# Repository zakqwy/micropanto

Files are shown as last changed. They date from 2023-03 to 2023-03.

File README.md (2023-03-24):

# MicroPanto

MicroPanto is a 50:1 pantograph reducer that converts a desktop CNC router into a micro-engraver. The machine is driven by a [Handibot](https://www.shopbottools.com/products/handibot), whose working range is shrunk to a few millimeters with a corresponding increase in resolution. A microswitch temporarily mounted to the Handibot's Z-axis actuates a stylus which can be electronically adjusted for different workpiece heights. The working tool is a laser-turned diamond bonded to a strip of stainless shim stock with a tip radius of roughly 2 microns. After assembling the machine at Haystack, a number of substrates (polished stone, steel, obsidian, gold-coated glass, silver, rice, etc) were micro-engraved with tiny messages and designs.

[project video link](https://player.vimeo.com/video/579890845) (thanks Jack!)

[a more detailed engraving video](https://youtu.be/u6EFz45_r_Y)

_Machine temporarily installed in the Haystack Metal Shop:_
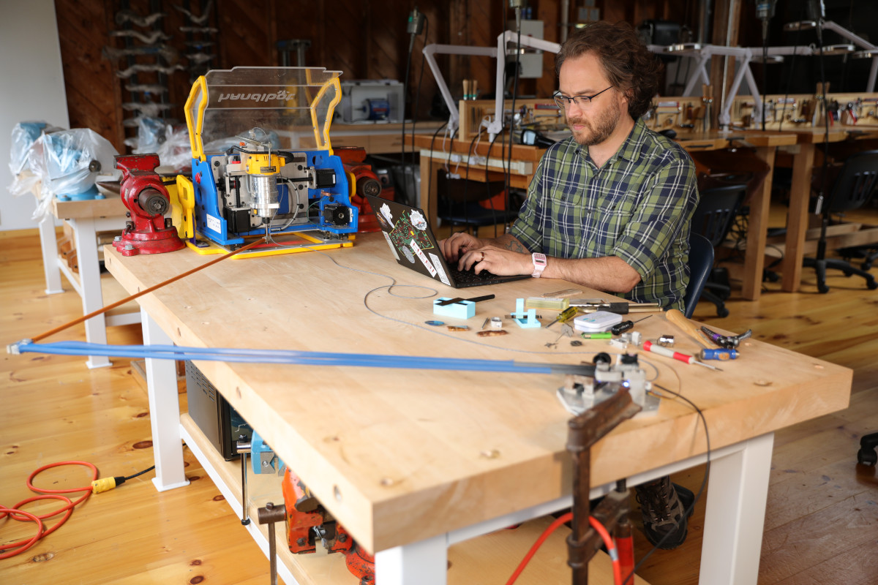
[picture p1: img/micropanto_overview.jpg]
micropanto_overview


_"Too Many Potatoes" engraved on a gold-coated slide, with 1/64" end mill for scale:_
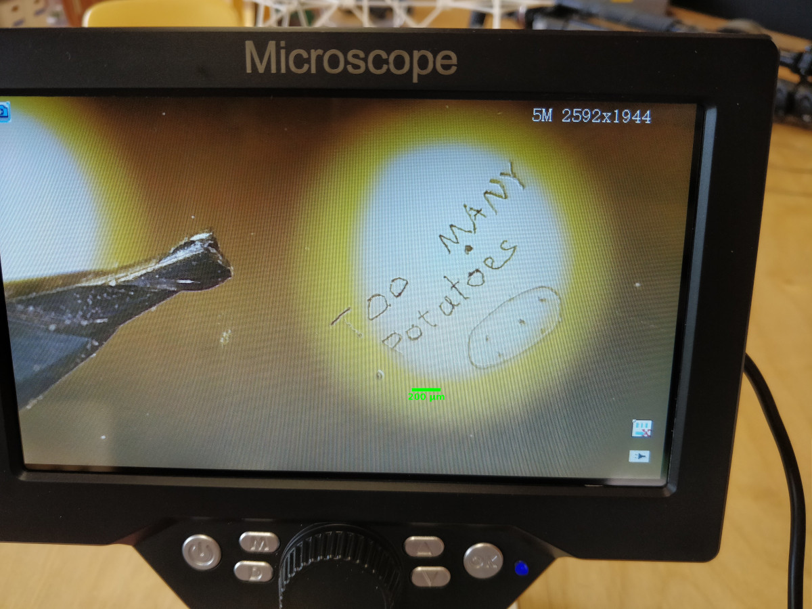
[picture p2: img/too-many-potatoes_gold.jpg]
too-many-potatoes_gold


_Stylus end showing base plate, work in vise, servo for stylus actuation, stylus control PCB, and modular superelastic flexure linkages:_
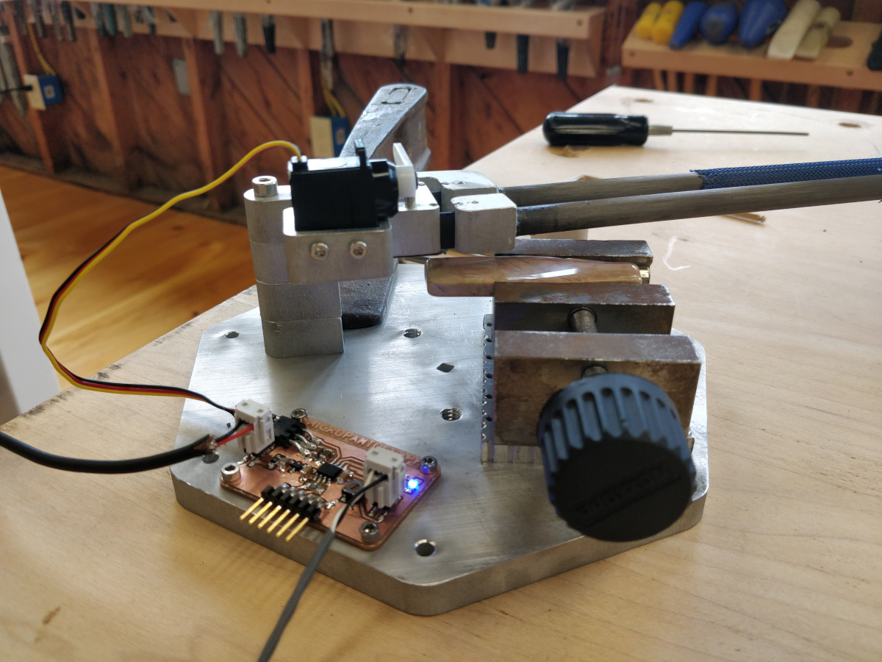
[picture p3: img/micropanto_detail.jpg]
micropanto_detail


This work may be reproduced, modified, distributed, performed, and displayed for any purpose, but must acknowledge the orginal project. Copyright is retained and must be preserved. The work is provided as is; no warranty is provided, and users accept all liability.

© zach fredin, massachusetts institute of technology, 2021

## micro-engraving
We tried micro-engraving a number of different things at Haystack. Here is a summary:

|thing|notes|
|---|---|
|gold-coated glass slide|Worked fairly well if stylus pressure was adjusted properly. Delicate during handling, somewhat impractical.|
|polished stone|Sourced from Ellen's collection (thanks Ellen!). Maybe picture jasper? Engraved fairly well, a bit of chipping if pressure too high. Required inking to see marks.|
|obsidian|Chips quite a bit. Looks promising if pressure can be better controlled; not great as-is.|
|aluminum|Snapped the diamond off the stylus! Likely an epoxy problem rather than a material issue; diamond re-affixed with CA and no further breakages.|
|silver|Looks _great_, especially if silver is polished and patinaed prior to marking.|
|black oxide coated steel|Tested on a few pairs of parallel-jaw pliers. Looks good, excellent detail.|
|pearl|Roundness is challenging. Needs careful pressure control to avoid over-engraving. Not great with current stylus design.|
|dry rice|Shockingly good, but did require inking afterwards. Maybe the marks would pick up extra staining in a pilaf and become visible (and stay edible)?|
|painted steel|i.e Zach's new glasses frames. Worked fairly well, paint was a bit thick which affected resolution. Underlying scratches on steel base are probably quite fine.|
|brushed stainless|Excellent detail; difficult to see.|

Perhaps not surprisingly, the 50:1 reduction ratio combined with my hesitency to push the machine's working range meant many of the engravings were quite difficult to see, even with a 10x loupe. Neil brought a cheap electronic microscope which I photographed; in retrospect, I should have found a micro SD card and pulled images directly off the instrument. Jack also got a few pictures with his amazing macro lens setup. As I find time, I'll use our instruments at CBA to get better images and update the gallery below.

_"The Center for Bits 'n Atoms", poorly mouse-drawn on the Handibot's SmoothSketch App:_
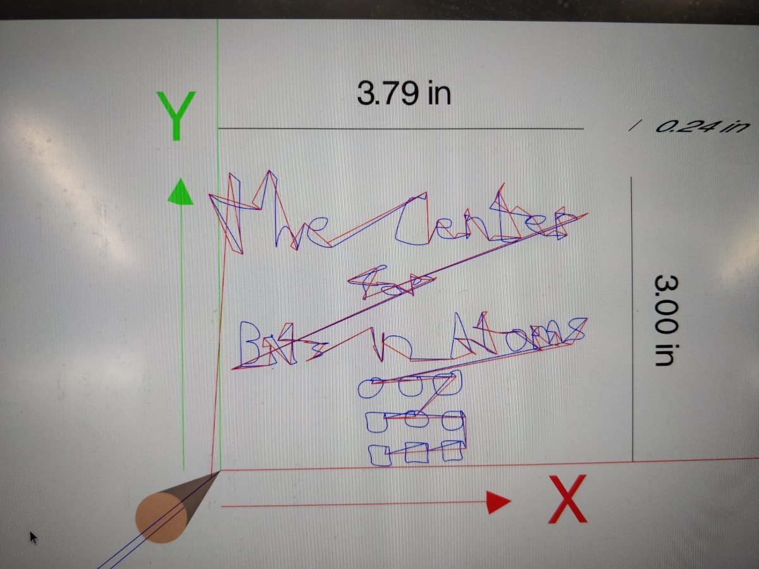
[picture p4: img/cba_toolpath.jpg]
cba_toolpath


_The resulting engraving on polished stone, after inking to add contrast. The "o" in Atoms is roughly 100 microns in diameter, the same as a typical strand of hair:_
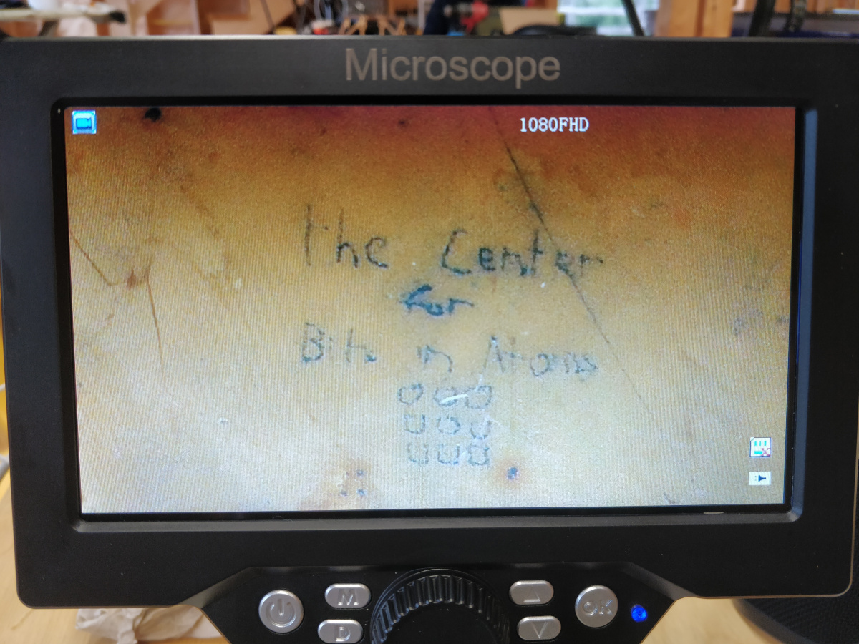
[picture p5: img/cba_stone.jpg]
cba_stone


_"Too Many Potatoes" rendered in inked stone:_
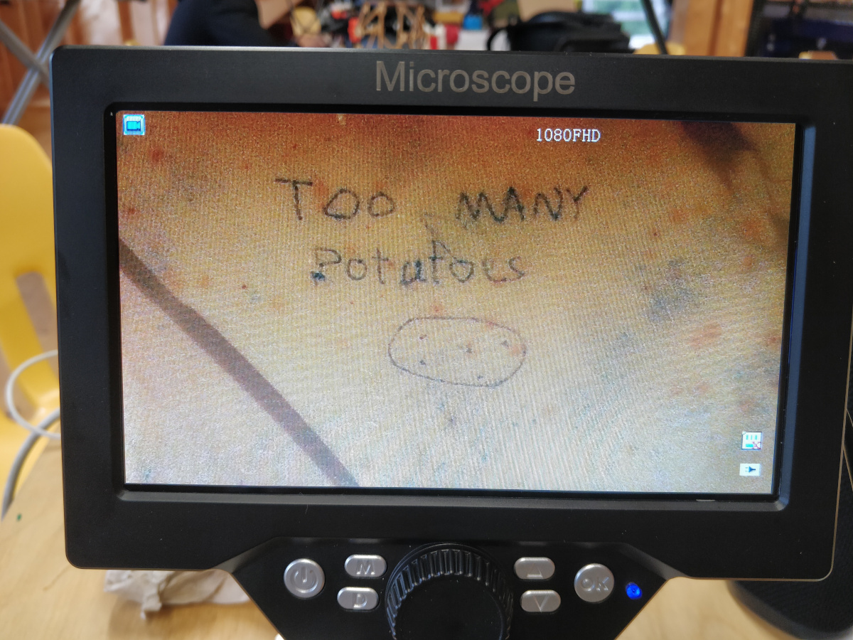
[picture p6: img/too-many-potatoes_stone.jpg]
too-many-potatoes_stone


_One of Andrea Dezsö's Forest Beings in gold-coated glass:_
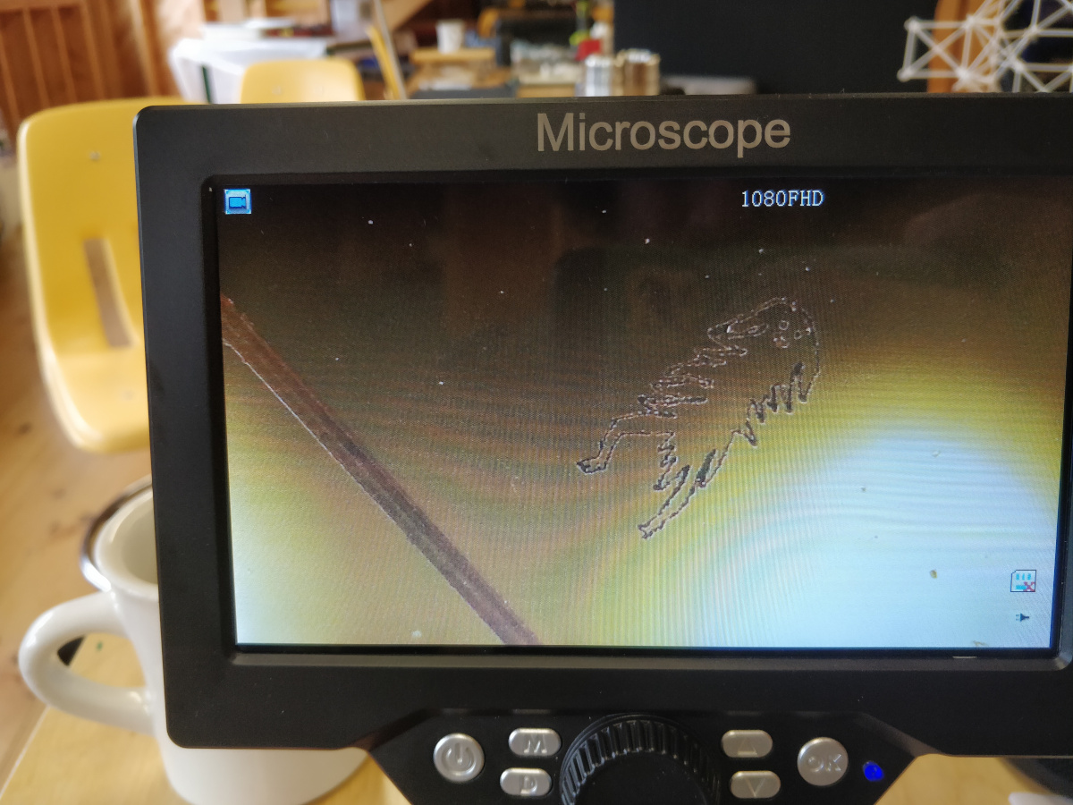
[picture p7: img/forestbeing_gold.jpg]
forestbeing_gold


_... and again in inked stone:_
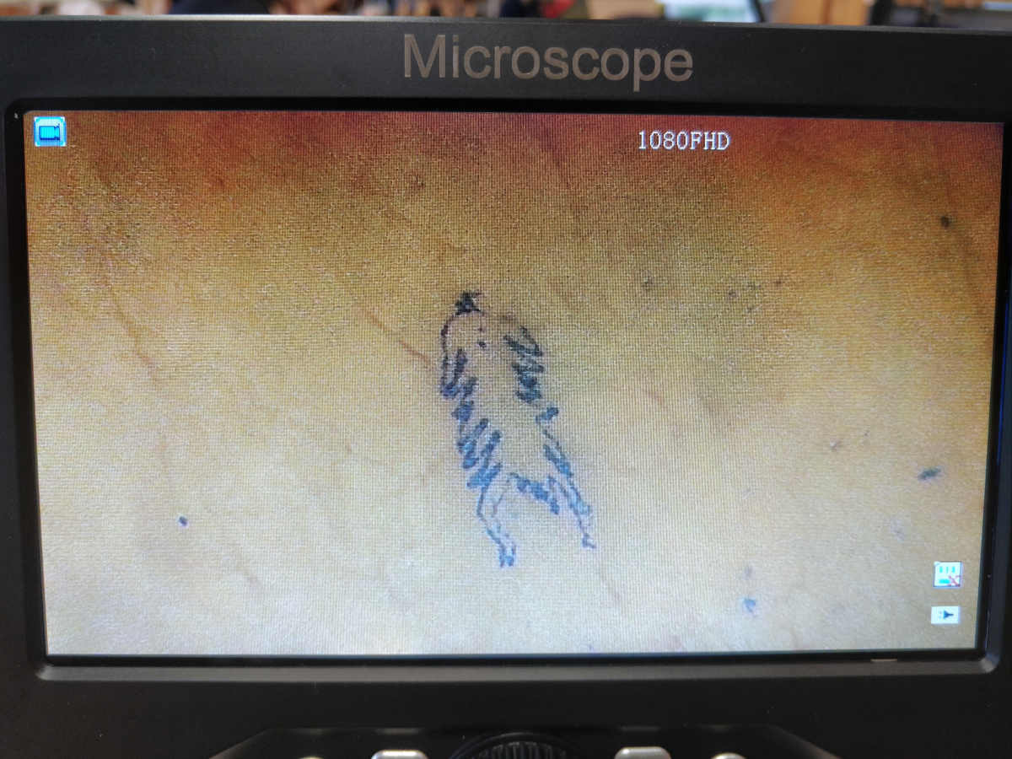
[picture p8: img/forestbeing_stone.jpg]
forestbeing_stone


_... and finally on grains of inked rice, along with a "HAYSTACK" sign:_
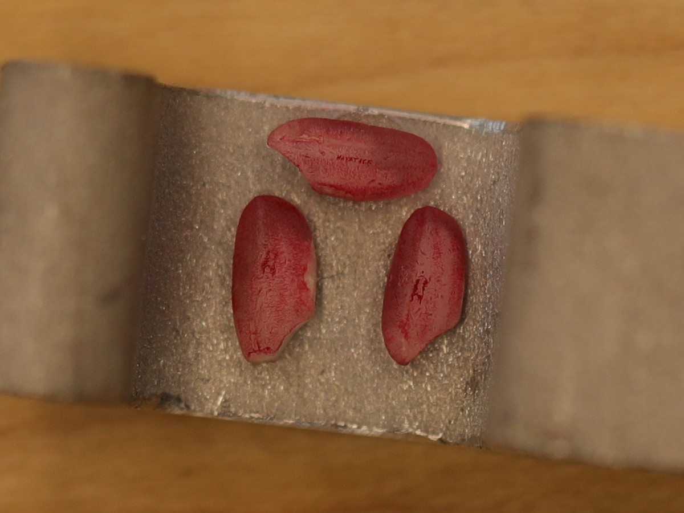
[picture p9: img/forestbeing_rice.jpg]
forestbeing_rice


_A Haystack welcome message (and another CBA "logo") in inked stone:_
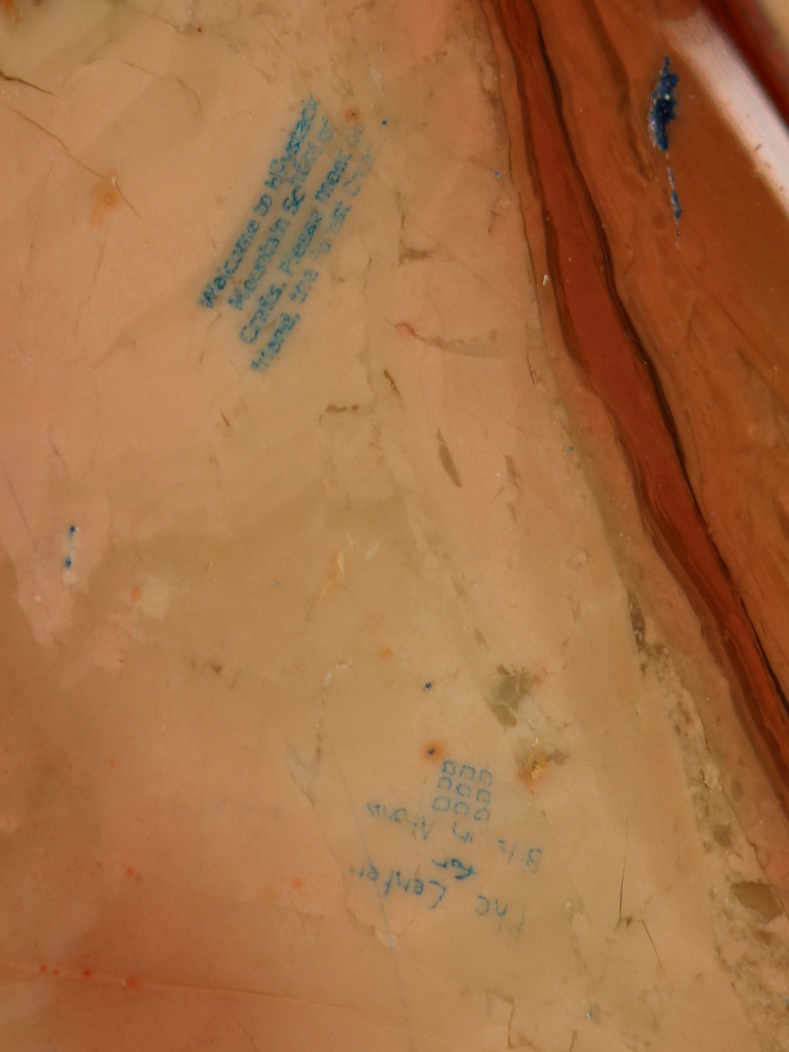
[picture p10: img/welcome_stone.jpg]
welcome_stone


_Lauren Fensterstock's black hole drawing, later micro-engraved on a number of substrates:_
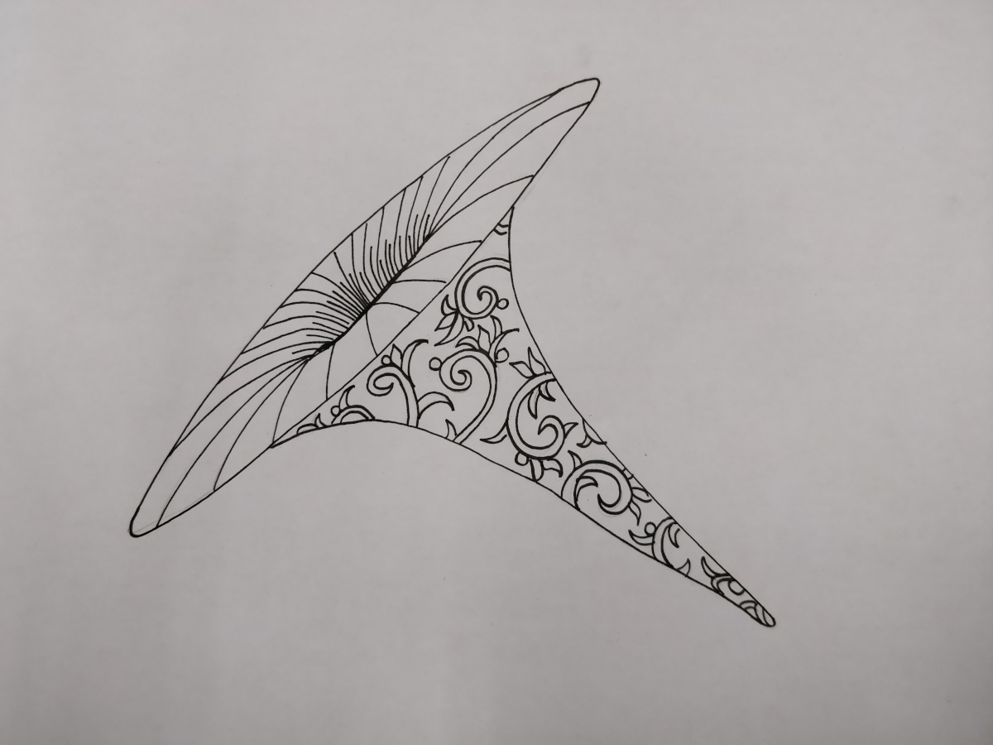
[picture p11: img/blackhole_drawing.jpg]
blackhole_drawing


_Black hole rendered on parallel-jaw pliers, with scale bar:_
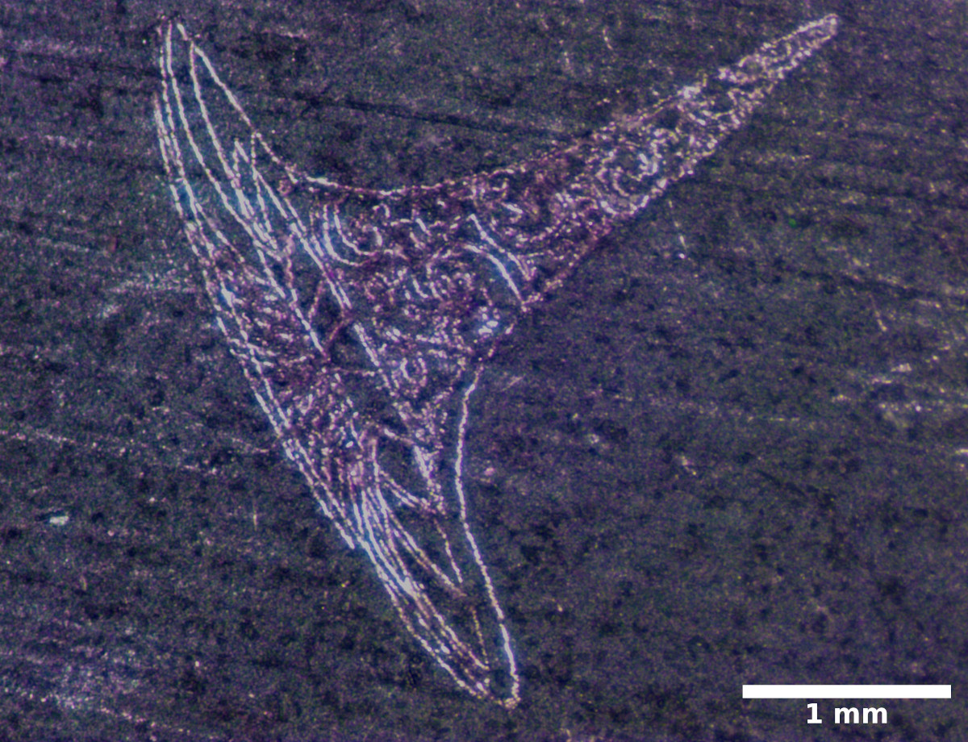
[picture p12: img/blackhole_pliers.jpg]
blackhole_pliers


_Zoomed out black hole for reference:_
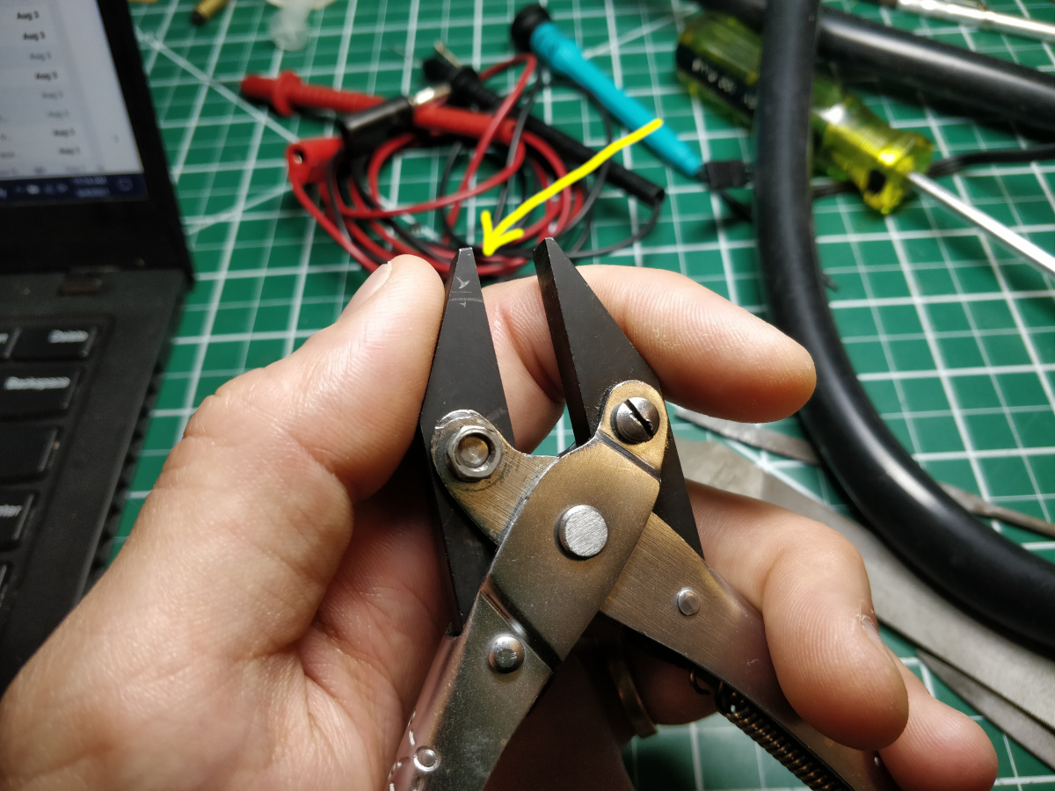
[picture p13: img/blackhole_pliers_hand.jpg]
blackhole_pliers_hand


_"Too Many Potatoes" on my new glasses frames, without magnification to show scale:_
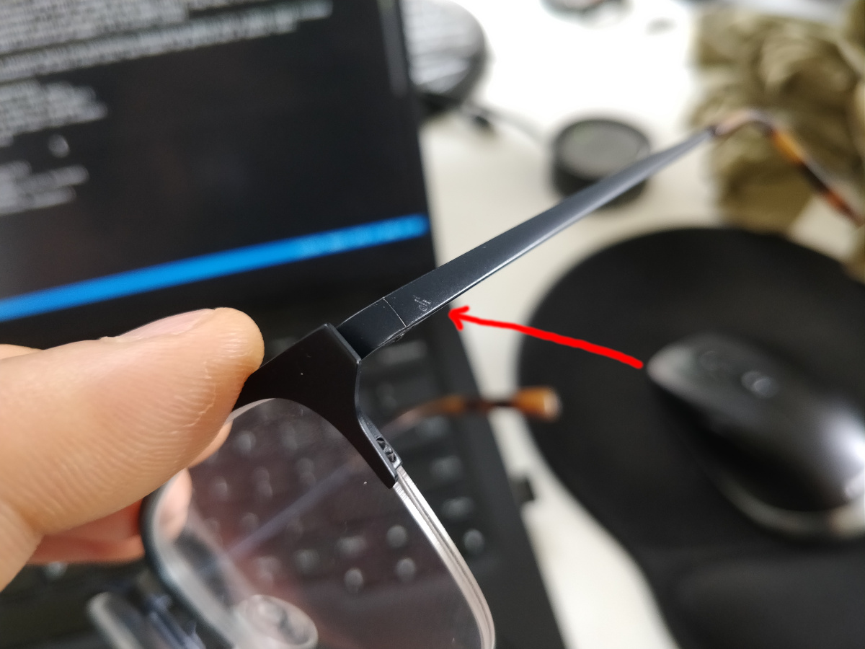
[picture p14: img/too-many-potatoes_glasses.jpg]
too-many-potatoes_glasses


## machine design
More information forthcoming... for now, [ecad](ecad) for the stylus control PCB, [firmware](firmware) for the stylus control firmware, and [mcad](mcad) for the mechanical design files. Parts are fabricated as follows:

|part|method|
|---|---|
|aluminum structural parts|waterjet, drill press|
|nitinol flexures|wire-EDM|
|stylus flexure|laser micro-machining|
|diamond stylus|laser micro-turning|
|PCB|desktop router, soldering iron|
|gold-coated slides|sputter coater|
|slide case|FDM 3D printer|
|pulltruded CFRP tubes|purchased|
|final machine assembly|taper ream, ball-peen hammer, epoxy|

The machine is built from modular superelastic flexures, a concept I developed as part of a class last semester. You can read a lot more about them [here](https://fab.cba.mit.edu/classes/865.21/people/zach/index.html). 

_Stylus detail, showing diamond in down position:_
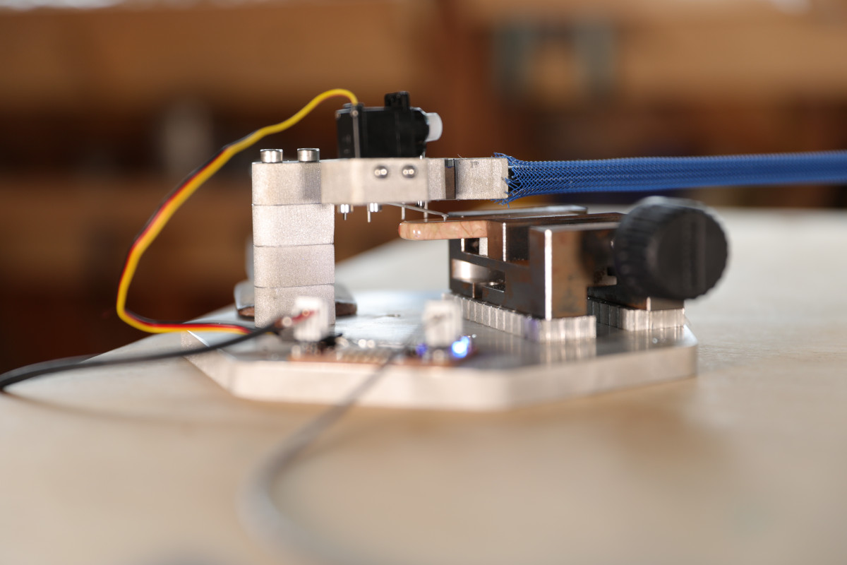
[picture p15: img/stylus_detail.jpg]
stylus_detail


_Final assembly starts with taper-reaming the waterjetted aluminum parts to match the nitinol flexures:_
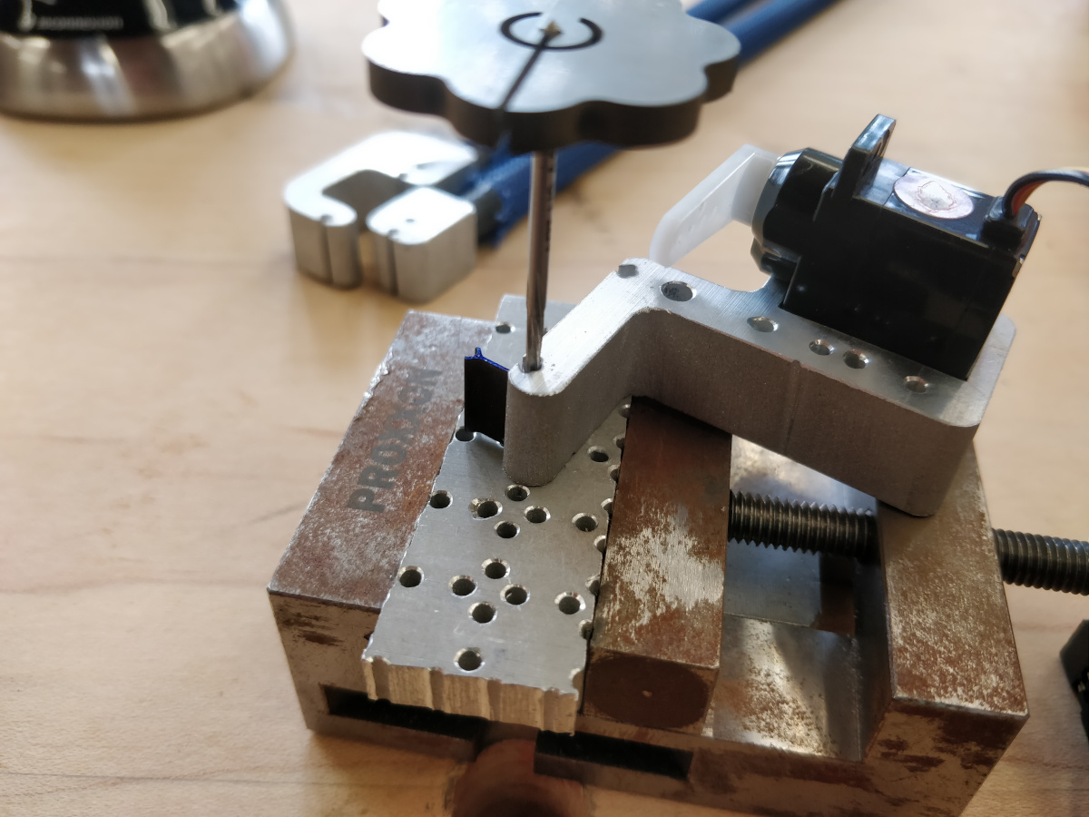
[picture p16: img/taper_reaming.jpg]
taper_reaming


_Once prepared, the joints are assembled by tapping in 7/0 taper pins with a ball peen hammer:_
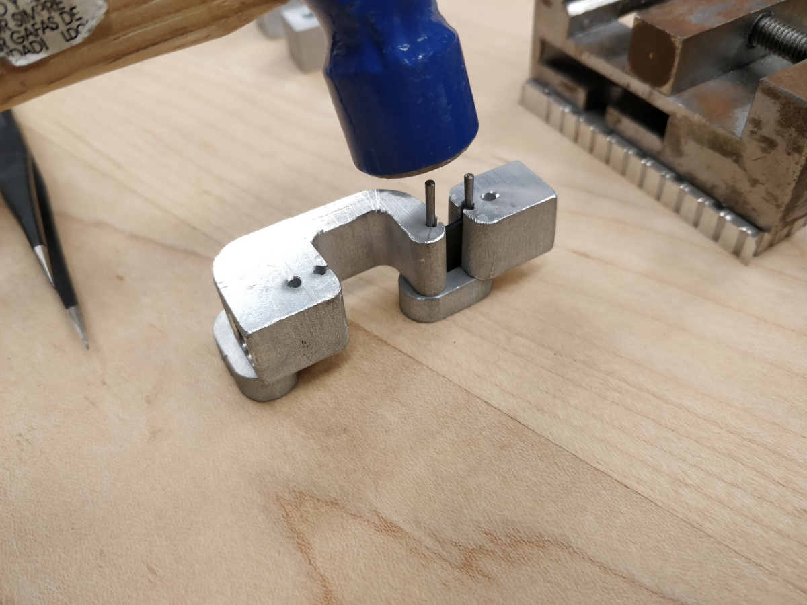
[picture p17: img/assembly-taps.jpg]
assembly_taps


_Disassembled stylus flexure and diamond (near tweezer tip) after breakage due to adhesive failure. Re-secured with cyanoacrylate, which worked well:_
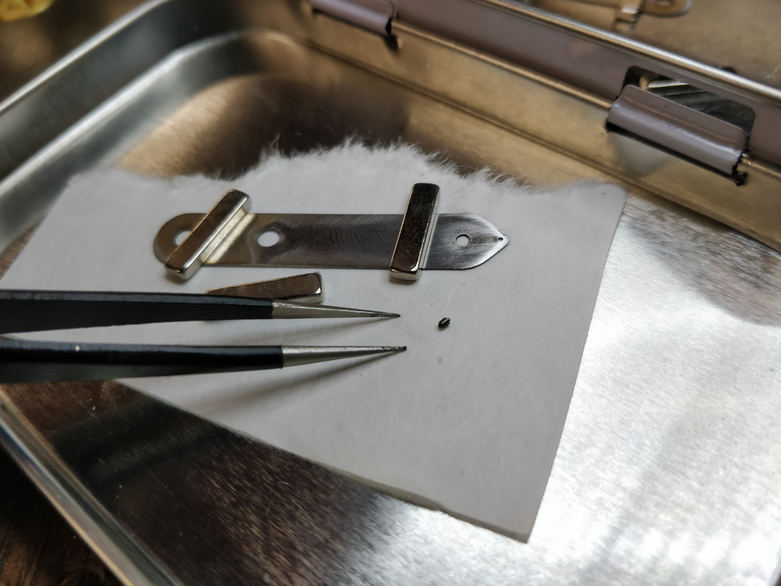
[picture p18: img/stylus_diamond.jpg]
stylus_diamond


_SEM micrograph of laser-turned diamond stylus, showing rough cut overall shape and finish pass at tip:_
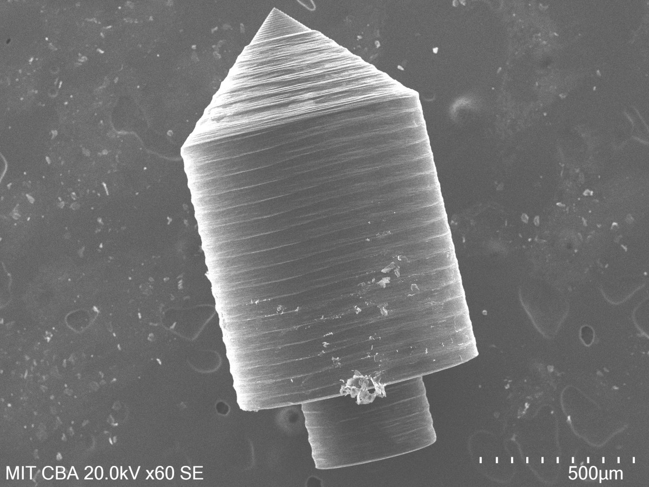
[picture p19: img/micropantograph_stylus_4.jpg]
micropantograph_stylus_4


_Another micrograph of the tip of the diamond, showing ~2 um tip radius. Would be worth re-imaging a used tip to see how it wears when used on different substrates:_
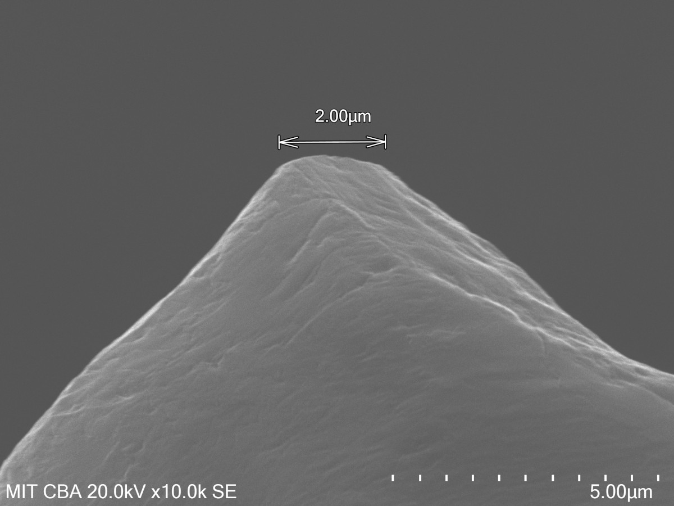
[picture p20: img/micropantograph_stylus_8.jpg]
micropantograph_stylus_8


MicroPanto roughly consists of:

|item|qty|
|---|---|
|aluminum plate, 1/2"|~75 x 75 mm|
|aluminum plate, 1/4"|~150 x 150 mm|
|aluminum plate, 1/16"|~10 x 80 mm|
|8 mm pulltruded CFRP tube|qty 3, 1 m|
|superelastic nitinol, 10 mm|~1 cc|
|bolts|~10?|
|7/0 taper pins|10|
|FR1 PCB stock|~75 x 50 mm|
|single-crystal CVD diamond|~1 x 1 x 3 mm|
|250 um stainless sheet|~10 x 40 mm|
|4 mm dowel pin|1|
|small servo motor|1|
|cable|~3 m|
|limit switch|1|
|Handibot|1|
|ATtiny412 + support components|1|
|computer|1|
|1/4" x 1/4" magnets|2|
|epoxy|a few packets|
|cable loom (for CFRP splinter protection)|~3 m|
|1/4" shaft stock|~100 mm|
|tiny vise|1|

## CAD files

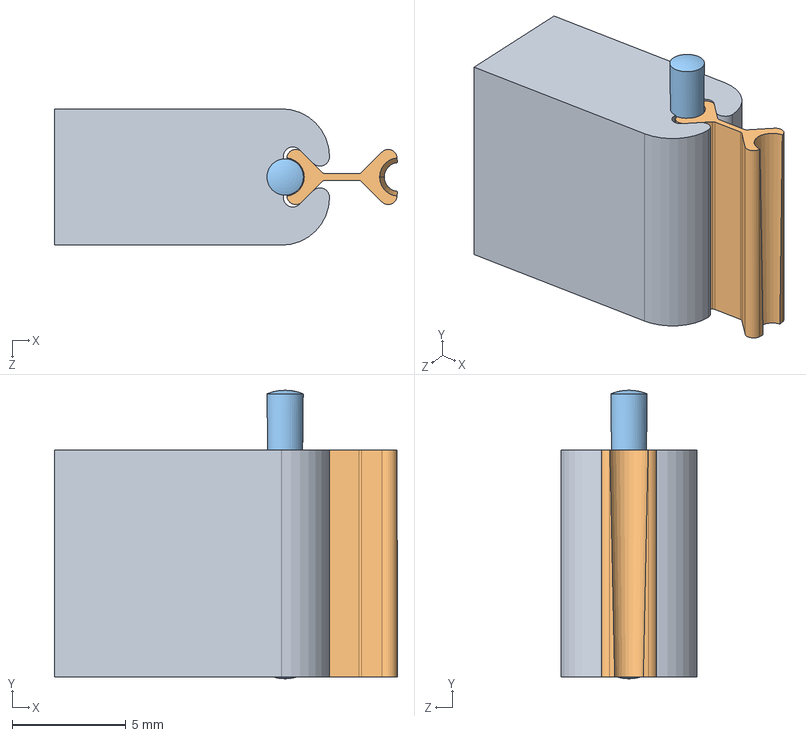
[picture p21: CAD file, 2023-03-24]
mcad/micropanto/diag.SLDASM
15.1 x 12.7 x 6.00 mm
link_long
bowtie_flexure
90681A001_18-8 STAINLESS STEEL TAPER PIN

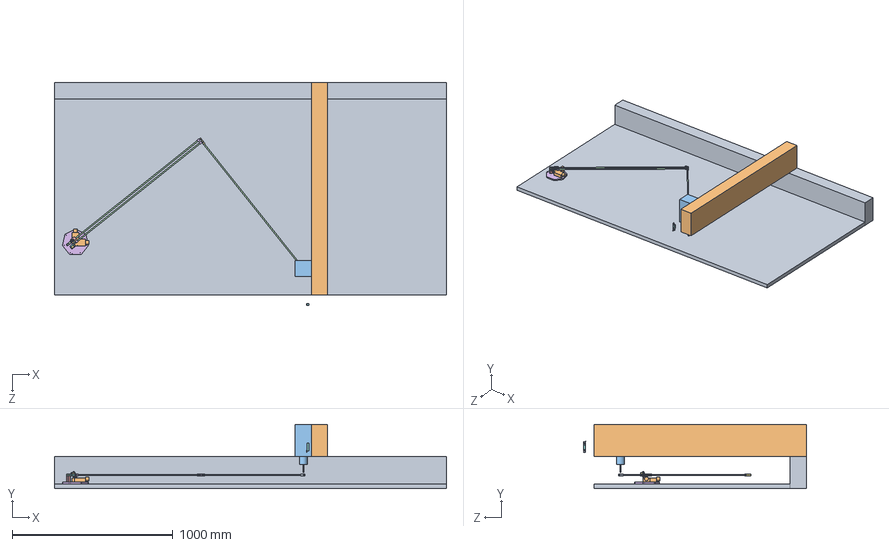
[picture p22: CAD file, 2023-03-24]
mcad/micropanto/micro-pantograph.SLDASM
2438.4 x 400.0 x 1384.9 mm
shopbot_base
shopbot_gantry
shopbot_spindle
rod_39in x 3
aluminum_adapter_1
aluminum_adapter_2 x 3
aluminum_adapter_3
aluminum_adapter_4
aluminum_adapter_5
bowtie_flexure_10_sim_part x 5
bowtie_flexure_10_sim_part2 x 5
aluminum_adapter_6
aluminum_adapter_7 x 3
base
servo
limitswitch_mount
limitswitch_bracket
proxxon_24260 x 2

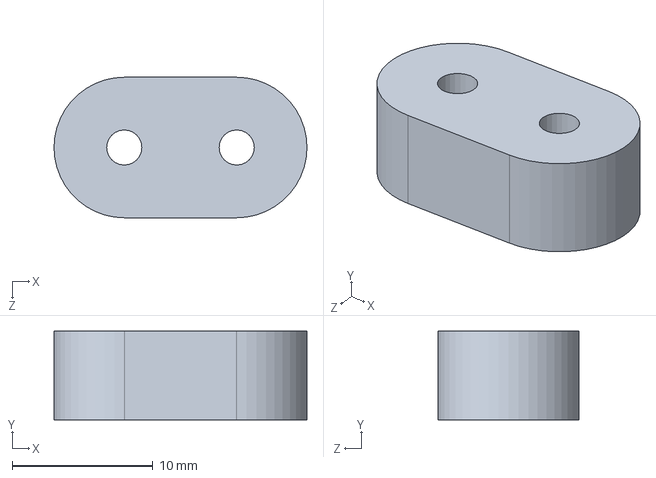
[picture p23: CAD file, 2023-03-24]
mcad/micropanto/assembly_helper.SLDPRT
18.0 x 6.30 x 10.0 mm

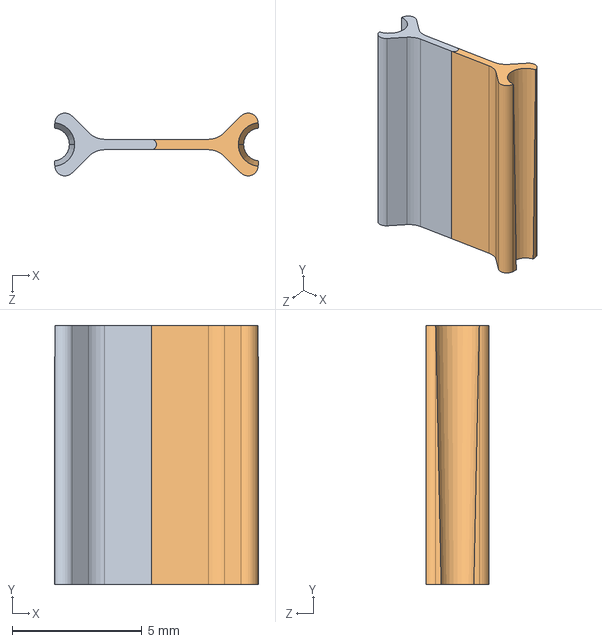
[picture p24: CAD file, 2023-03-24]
mcad/micropanto/bowtie_flexure_10_sim_assembly.SLDASM
7.89 x 10.0 x 2.43 mm
bowtie_flexure_10_sim_part
bowtie_flexure_10_sim_part2

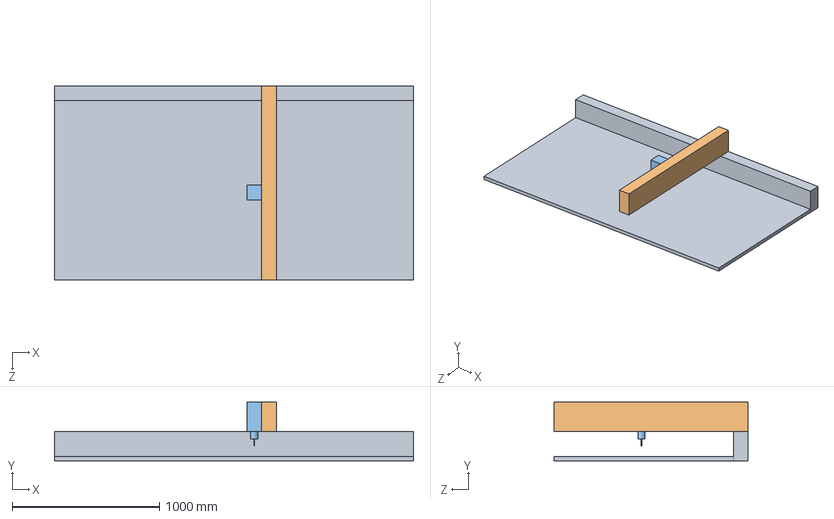
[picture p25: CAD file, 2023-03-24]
mcad/micropanto/shopbot.SLDASM
2438.4 x 400.0 x 1320.8 mm
shopbot_base
shopbot_gantry
shopbot_spindle

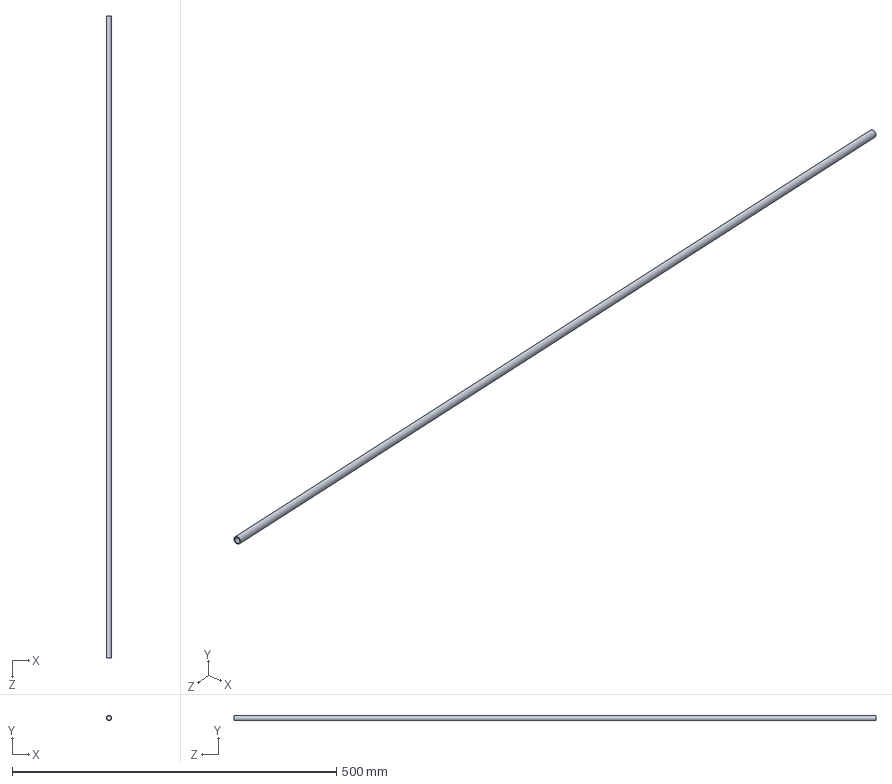
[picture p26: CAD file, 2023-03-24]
mcad/micropanto/rod_39in.SLDPRT
8.00 x 8.00 x 990.6 mm

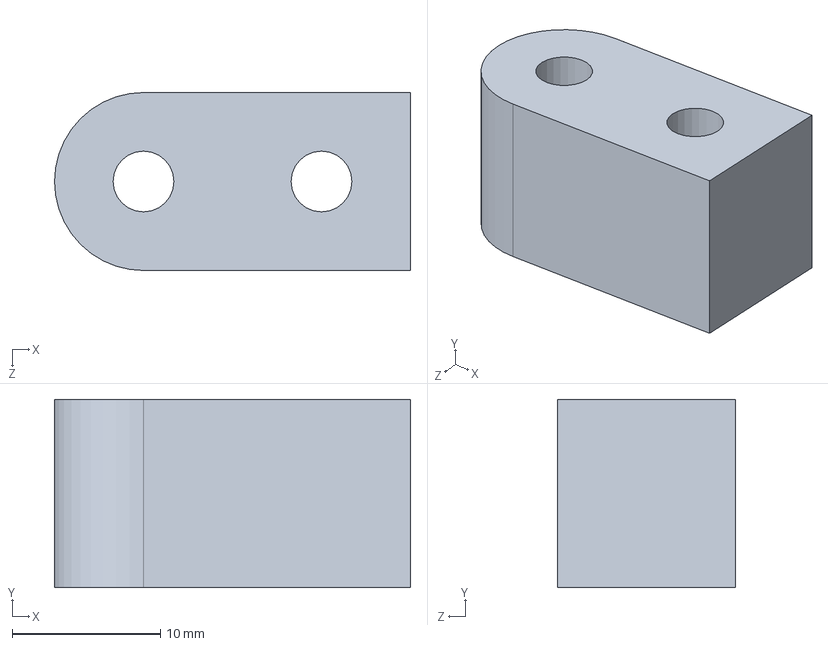
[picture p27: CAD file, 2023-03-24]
mcad/micropanto/aluminum_adapter_7.SLDPRT
24.0 x 12.7 x 12.0 mm

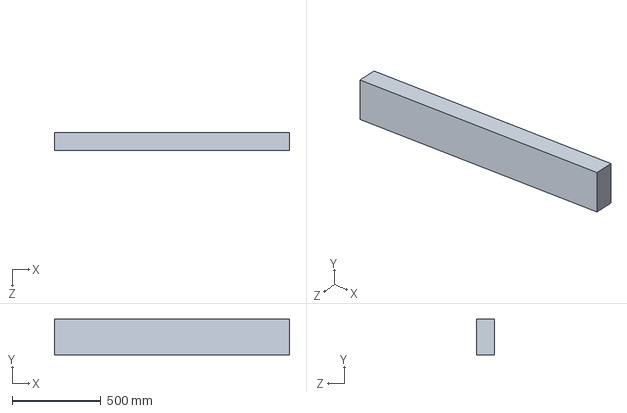
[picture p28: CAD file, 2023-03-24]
mcad/micropanto/shopbot_gantry.SLDPRT
1320.8 x 200.0 x 100.0 mm

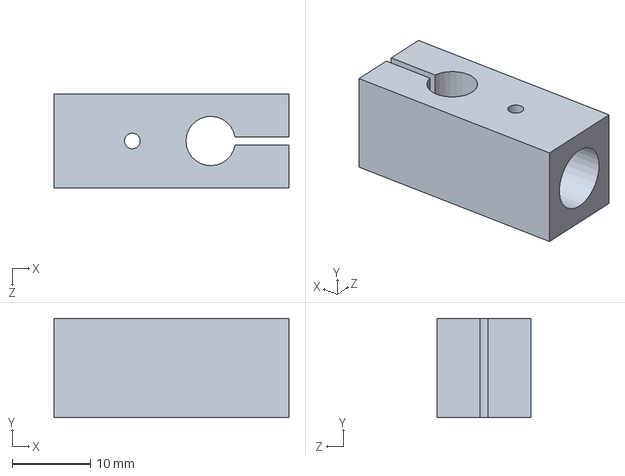
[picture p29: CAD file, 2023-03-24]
mcad/micropanto/aluminum_adapter_5.SLDPRT
30.0 x 12.7 x 12.0 mm

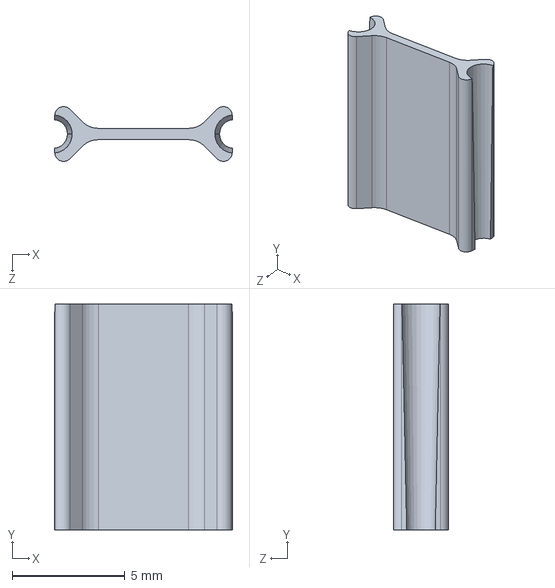
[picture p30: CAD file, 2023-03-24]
mcad/micropanto/bowtie_flexure_10.SLDPRT
7.89 x 10.0 x 2.43 mm

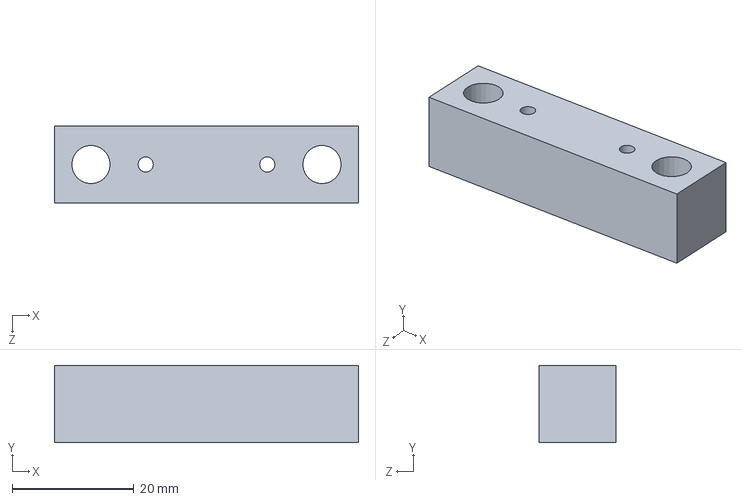
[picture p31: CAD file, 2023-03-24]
mcad/micropanto/limitswitch_mount.SLDPRT
50.0 x 12.7 x 12.7 mm

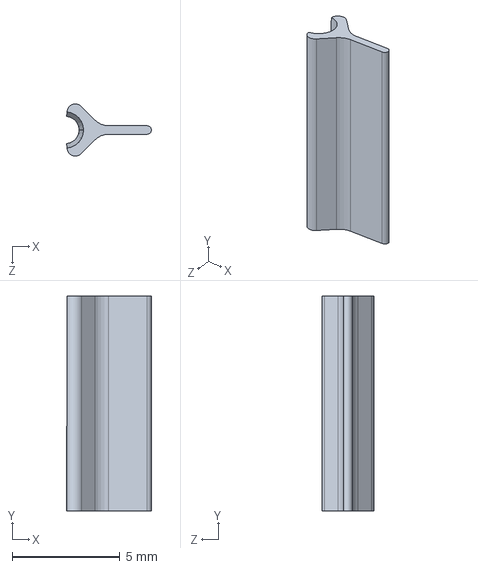
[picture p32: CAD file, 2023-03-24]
mcad/micropanto/bowtie_flexure_10_sim_part.SLDPRT
3.94 x 10.0 x 2.43 mm

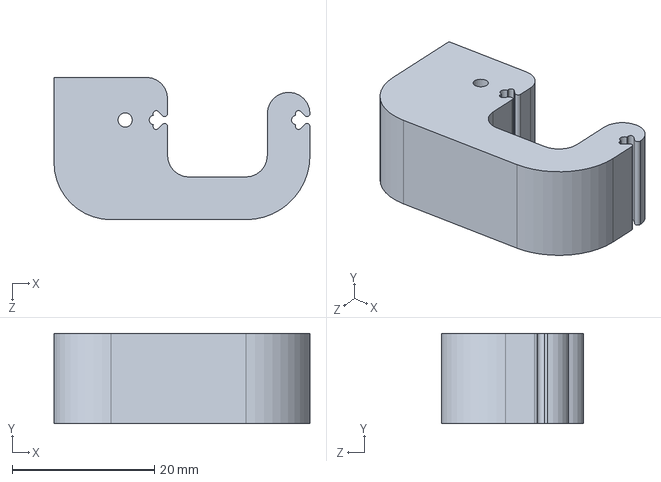
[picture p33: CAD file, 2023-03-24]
mcad/micropanto/aluminum_adapter_1.SLDPRT
36.0 x 12.7 x 20.0 mm

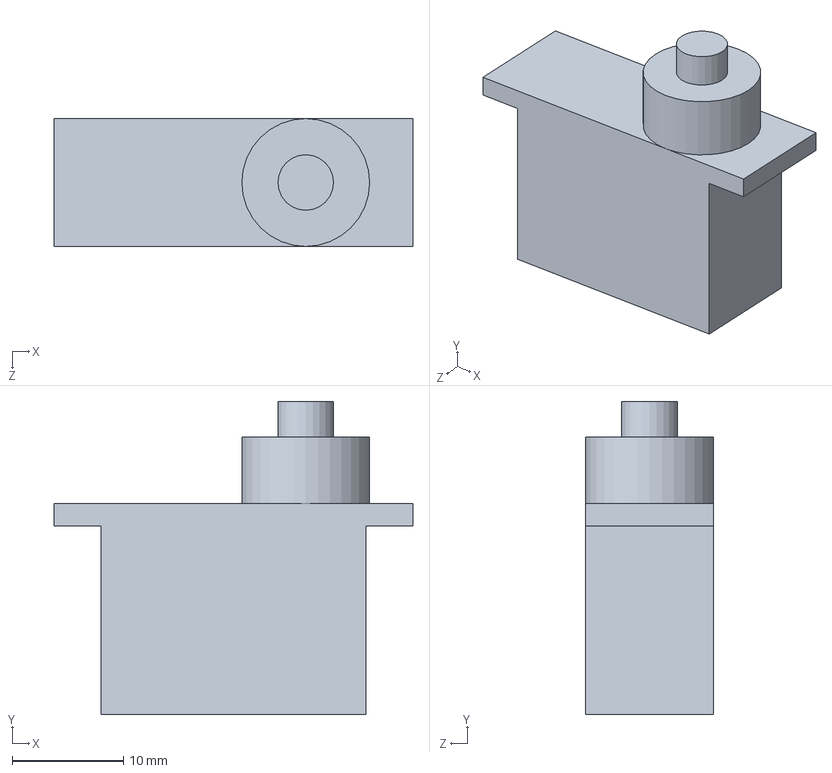
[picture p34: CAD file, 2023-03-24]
mcad/micropanto/servo.SLDPRT
32.3 x 28.2 x 11.5 mm

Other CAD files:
mcad/micropanto/base.SLDPRT
mcad/micropanto/slidebox_bottom.SLDPRT
mcad/micropanto/bowtie_flexure_10_sim_part2.SLDPRT
mcad/micropanto/slidebox_top.SLDPRT
mcad/micropanto/aluminum_adapter_2.SLDPRT
mcad/micropanto/aluminum_adapter_3.SLDPRT
mcad/micropanto/aluminum_adapter_4.SLDPRT
mcad/micropanto/aluminum_adapter_6.SLDPRT
mcad/micropanto/assembly_helper.DXF
mcad/micropanto/bowtie_flexure_10_combined.dxf
mcad/micropanto/bowtie_flexure_10_thk.SLDPRT
mcad/micropanto/bowtie_flexure_10_thk_combined.dxf
mcad/micropanto/limitswitch_bracket.SLDPRT
mcad/micropanto/proxxon_24260.SLDPRT
mcad/micropanto/shopbot_base.SLDPRT
mcad/micropanto/shopbot_spindle.SLDPRT
mcad/micropanto/slidebox_bottom.STL
mcad/micropanto/slidebox_top.STL

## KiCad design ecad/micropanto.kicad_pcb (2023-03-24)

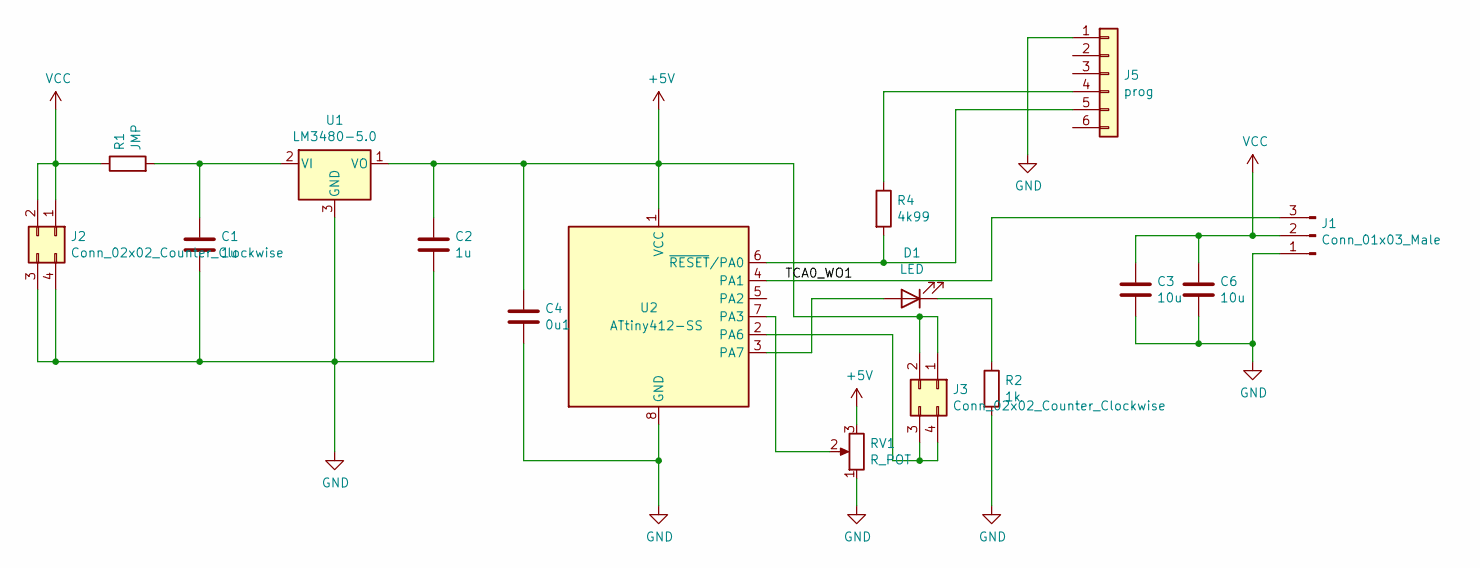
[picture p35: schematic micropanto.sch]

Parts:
C1, C2: 1u; fab_C_1206
C3, C6: 10u; fab_R_1206
C4: 0u1; fab_C_1206
D1: LED; fab_LED_1206
J1: Conn_01x03_Male; CONN_SERVO_SMT
J2, J3: Conn_02x02_Counter_Clockwise; PinHeader_2x02_P2.54mm_Vertical_SMD
J5: prog; fab_CONN_1x06_SMD
R1: JMP; fab_R_1206
R2: 1k; fab_R_1206
R4: 4k99; fab_R_1206
RV1: R_POT; Potentiometer_Bourns_3214G_Horizontal
U1: LM3480-5.0; fab_SMD_SOT23
U2: ATtiny412-SS; fab_IC_SOIC8

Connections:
+5V: C2.1, C4.1, J3.1, J3.2, RV1.3, U1.1 (VO), U2.1 (VCC)
/TCA0_WO1: J1.3, U2.4 (PA1)
GND: C1.2, C2.2, C3.2, C4.2, C6.2, J1.1, J2.3, J2.4, J5.1, R2.2, RV1.1, U1.3 (GND), U2.8 (GND)
unnamed: C1.1, R1.2, U1.2 (VI)
unnamed: D1.1 (K), R2.1
unnamed: D1.2 (A), U2.3 (PA7)
unnamed: J3.3, J3.4, U2.2 (PA6)
unnamed: J5.4, R4.1
unnamed: J5.5, R4.2, U2.6 (~RESET~/PA0)
unnamed: RV1.2, U2.7 (PA3)
VCC: C3.1, C6.1, J1.2, J2.1, J2.2, R1.1

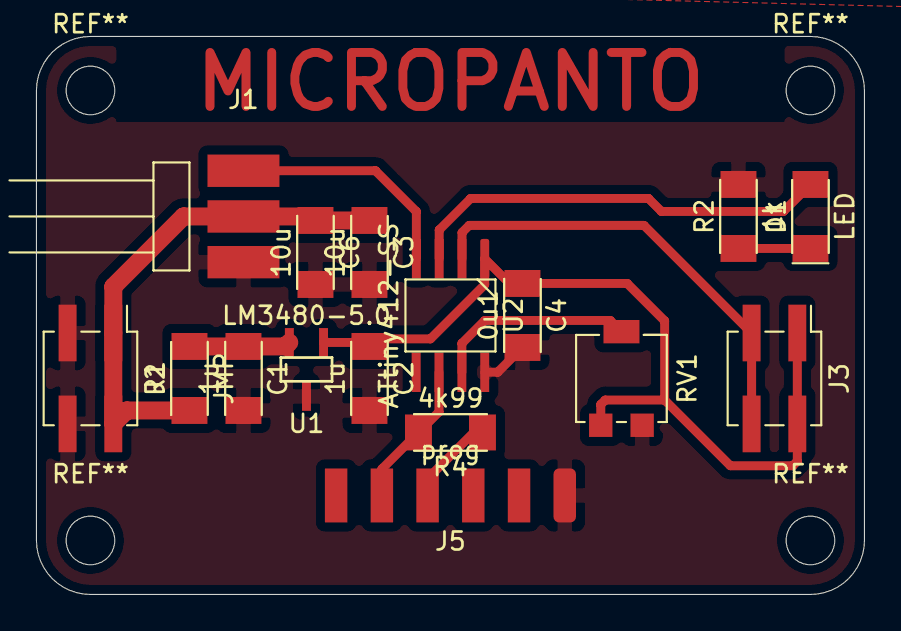
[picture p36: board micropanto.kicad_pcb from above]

Board: 2 copper layers, 46.0 x 31.0 mm, 16 parts (0 on the bottom side), 11 nets.

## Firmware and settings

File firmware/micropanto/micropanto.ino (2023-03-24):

#include <avr/io.h>

#define LED PIN7_bm
#define SERVO PIN1_bm
#define SENSE PIN6_bm
#define POT PIN4_bm

int servo_pos0 = 623; //down position, max 623
int servo_pos1 = 523; // up position

void setup() {
    // init _everything_ since reprogramming != reset
    TCA0.SINGLE.CTRLA = 0;
    TCA0.SINGLE.CTRLB = 0;
    TCA0.SINGLE.CTRLC = 0;
    TCA0.SINGLE.CTRLD = 0;

    // set up timer TCA for servo output on pin 4 / PA1 / W01
    TCA0.SINGLE.CTRLA |= ((1<<1) | (1<<3)); // fclk/64 (312.5 kHz)
    TCA0.SINGLE.PER = 6250; //pwm period = ~50 Hz
    TCA0.SINGLE.CMP1 = servo_pos0; //starting pulse width = 1.5 ms
    TCA0.SINGLE.CTRLB |= (1<<5); //enable compare TCA W01
    TCA0.SINGLE.CTRLB |= ((1<<0) | (1<<1)); //set TCA to single-slope PWM mode
    TCA0.SINGLE.CTRLA |= (1<<0); //enable timer TCA

    // GPIO setup
    PORTA.DIRSET = LED;
    PORTA.DIRSET = SERVO;
    PORTA.DIRCLR = SENSE;
    PORTA.DIRCLR = POT;
}


void loop() {
  servo_pos0 = map(analogRead(PIN_PA3),0,1023,523,623);
  PORTA.OUTSET = LED;
  if (PORTA.IN & SENSE) { //switch released, stylus up
    TCA0.SINGLE.CMP1 = servo_pos1;
  }
  else { //switch released, stylus down
    TCA0.SINGLE.CMP1 = servo_pos0;
  }
}
